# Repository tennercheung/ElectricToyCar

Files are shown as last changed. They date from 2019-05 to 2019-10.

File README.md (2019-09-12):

# ElectricToyCar

# (Car 1)
## ProtoV1

Code implemented with intent to test control with IR and on-board user controls of the vehicle

Encountered Issues:
* IR controls send different hex code stead FFFFFF when held in testing

## ProtoV1.1

Code implemented with intent to just the rider’s controls of the vehicle (speed & driving modes)

Encountered Issues:
* Motors shaking/jittery in fwd & bwd = PWM given to motor needs to start from low value so motors have time to speed up
* Motors run smoother independently -> since they are lower speeds there is less time needed to speed up
* When Arduino is reset, M2 is given power due to unallocated states of pins = since connected to LED takes a high during reset, reallocated pin 13 to pin 7

* Multiple buttons touched should keep system idle but instead triggers one/a mix of the button’s functions

## ProtoV2

Encountered Issues:
* Arduino must be **off** to send serial output to battery
* Battery has automatic shut off when pedal switch has not been pressed for longer than ~***10 minutes***
* When starting up the car, pedal switch is to be pressed first while the switch for power to the Arduino and H-Bridge (Red Switch on the back of the car) is off.
* 60kg servo does not function with the Arduino library, but works if it connects to the RC receiver
* Small servo jitters when RC is shut off
* Small detail, hidden speed control switch can be implemented as a small feature incase client wants to increase the speed of the car

# (Car 2)
## ProtoV1 
Encountered Issues: N/A

## Pedal Signal Analysis
Oscilloscope
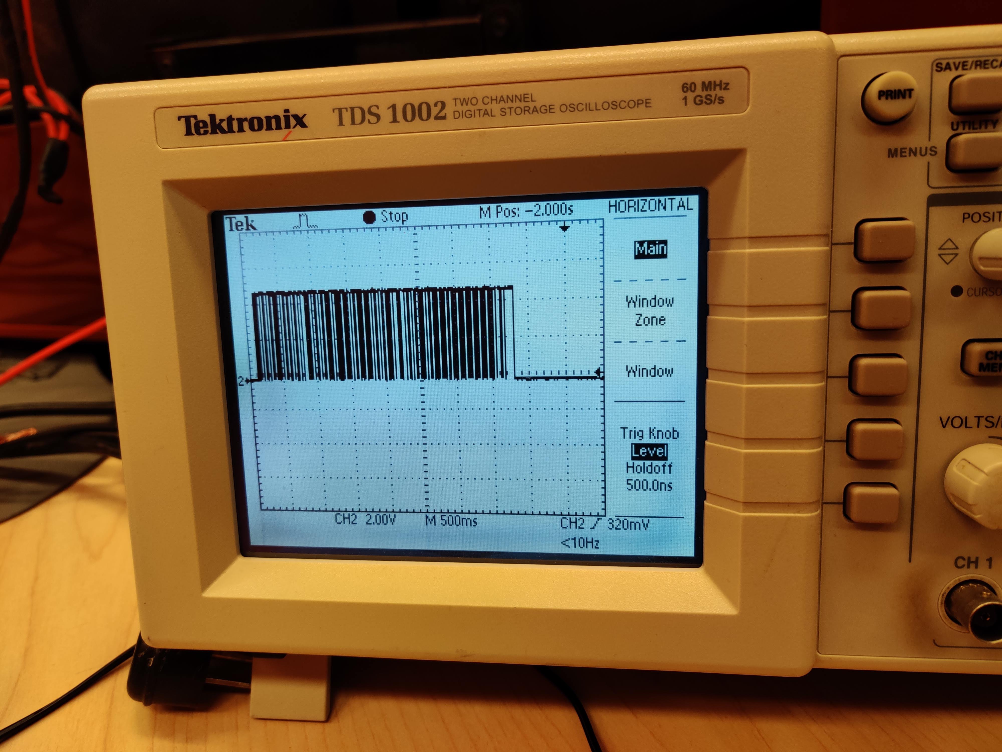
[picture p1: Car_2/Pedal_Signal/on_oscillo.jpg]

Serial Plotter
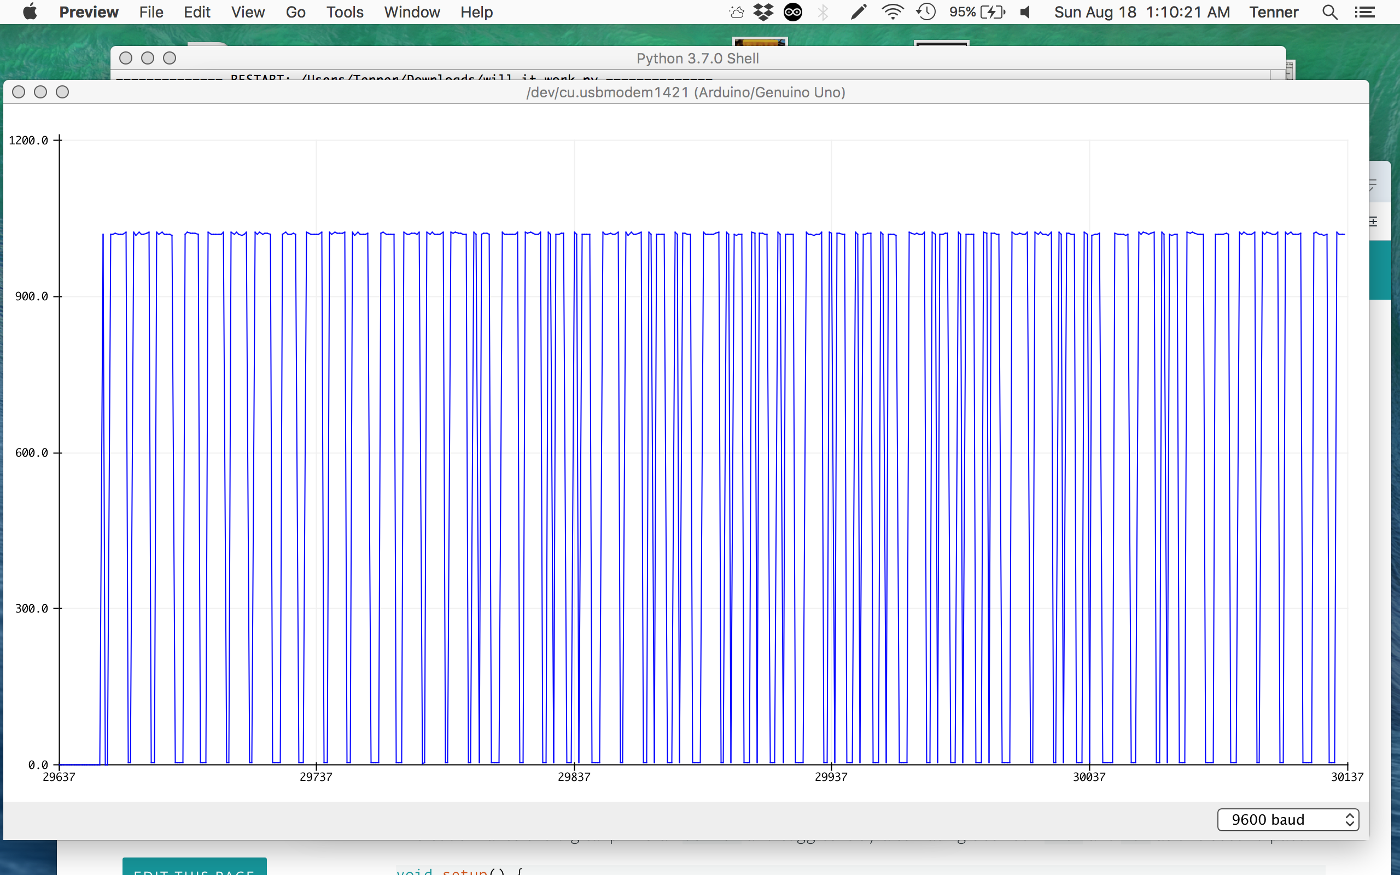
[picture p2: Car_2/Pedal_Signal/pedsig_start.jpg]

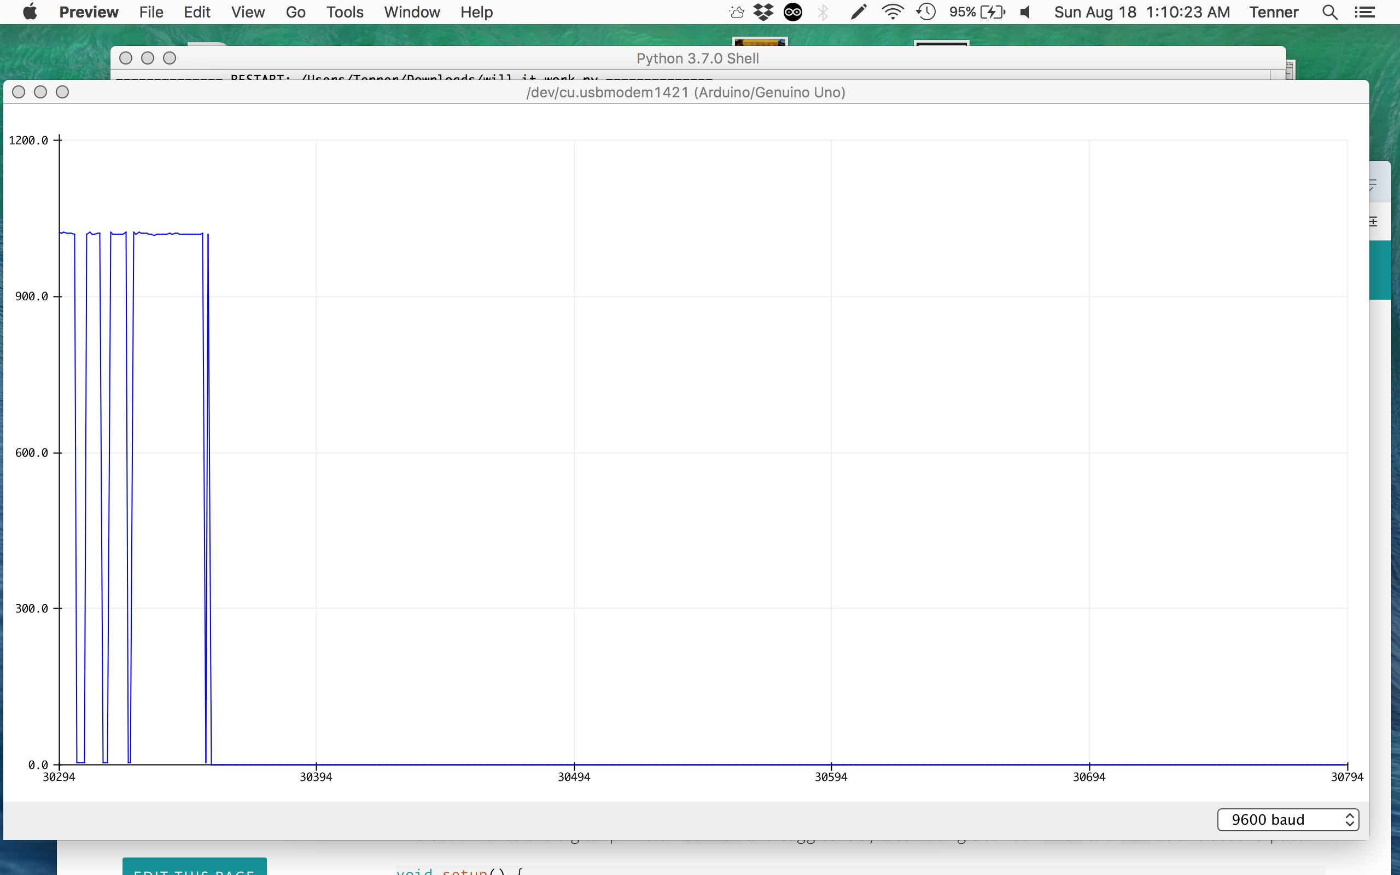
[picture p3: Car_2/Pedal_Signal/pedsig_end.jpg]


## Schematics

Motors
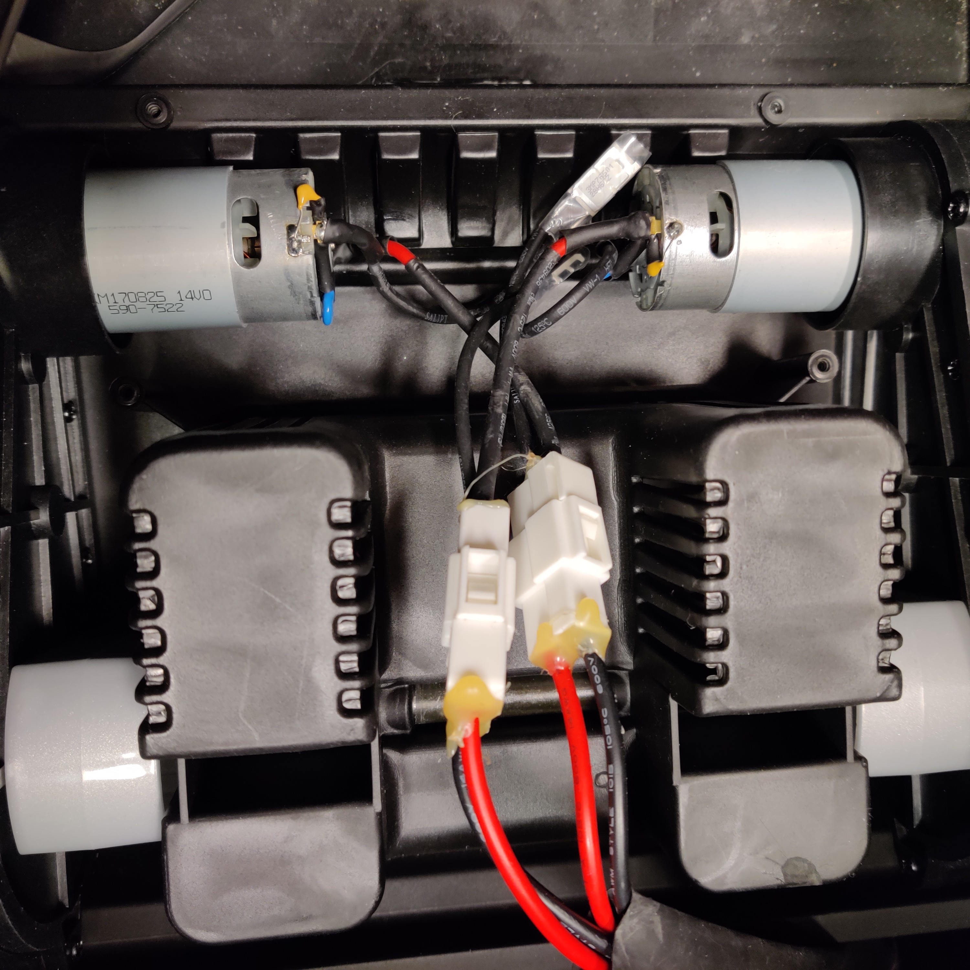
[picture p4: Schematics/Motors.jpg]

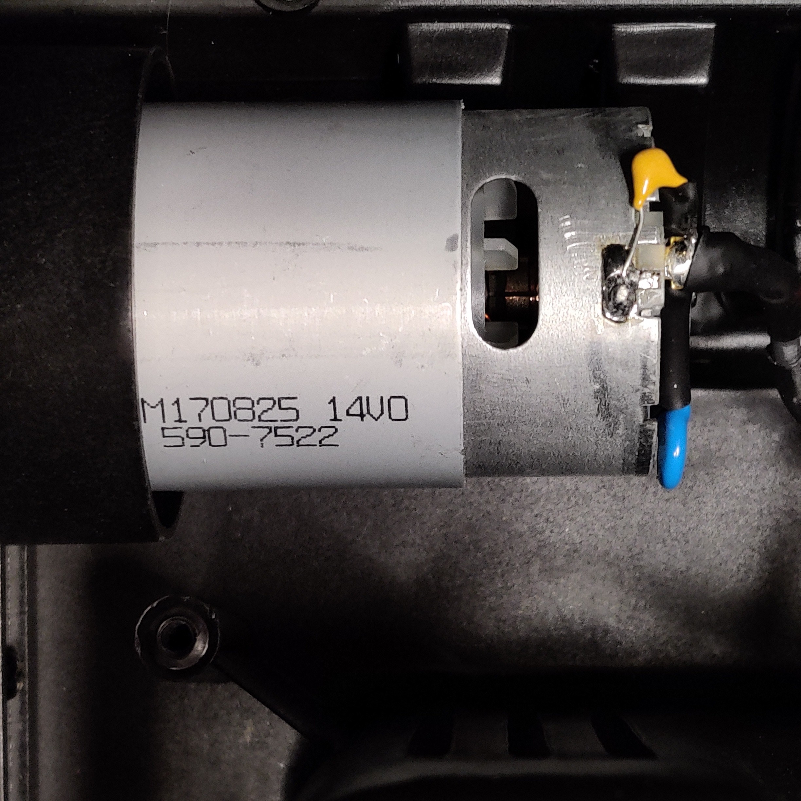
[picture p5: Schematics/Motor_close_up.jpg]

Dashboard PCB
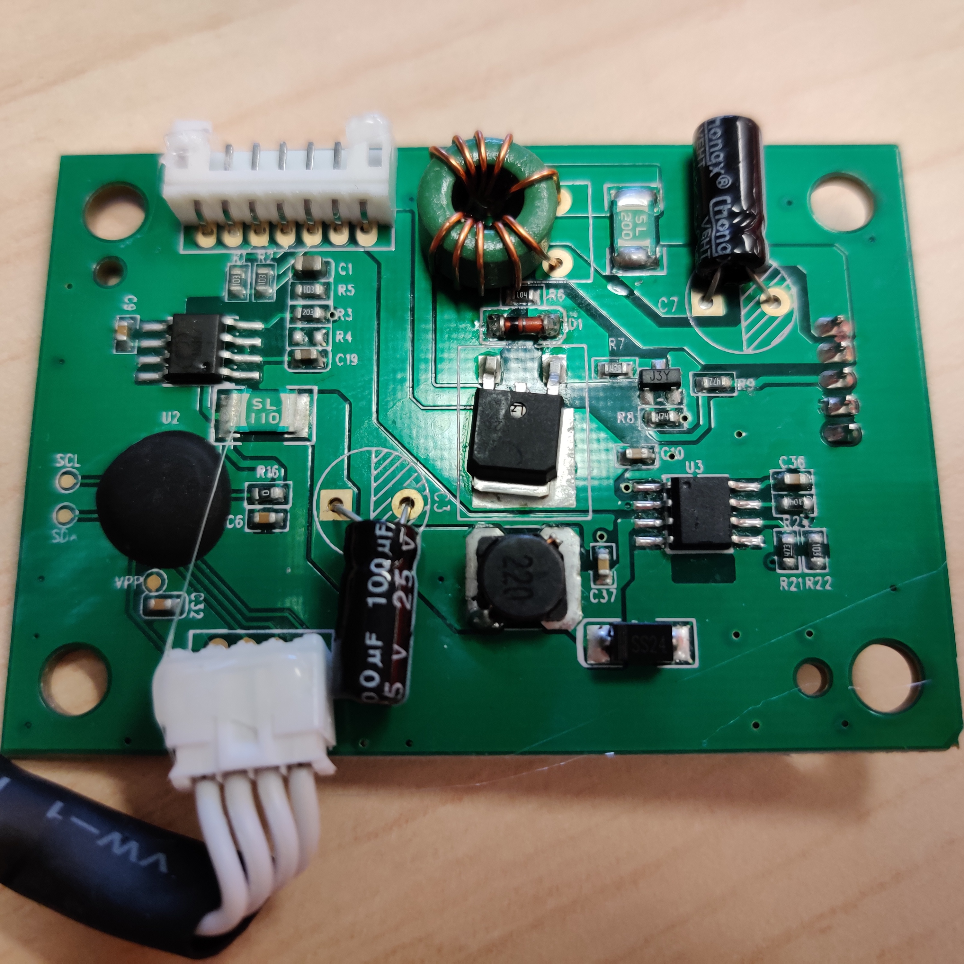
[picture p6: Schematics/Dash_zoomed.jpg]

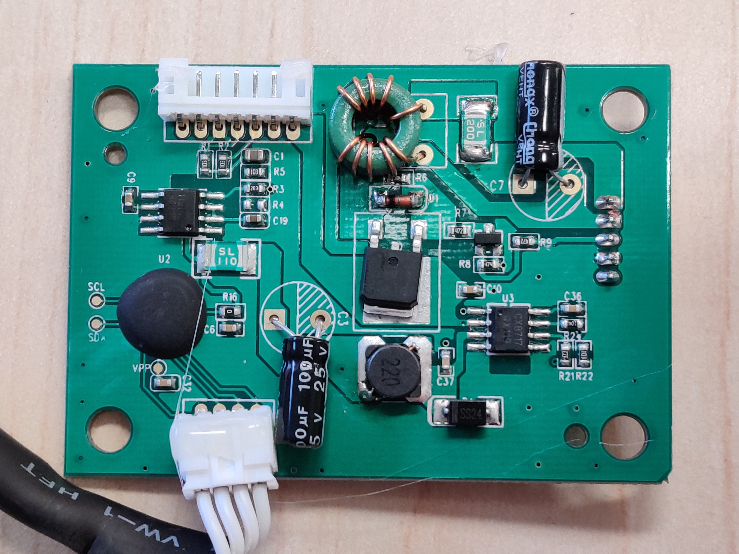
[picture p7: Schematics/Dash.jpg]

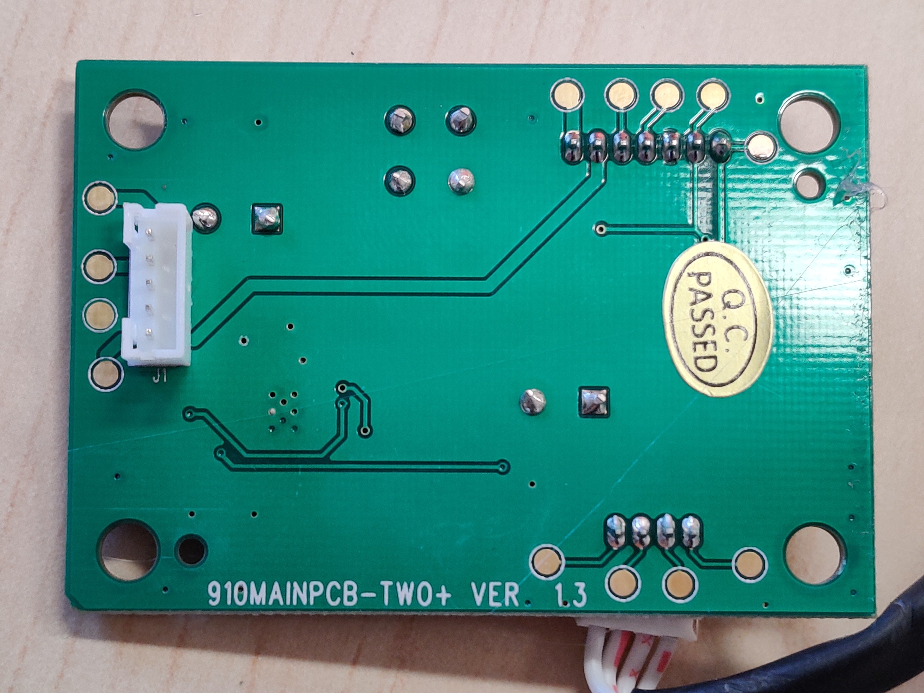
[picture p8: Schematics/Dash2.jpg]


## Useful Links:
* 7A/160W L298 Motor Board (https://amzn.to/2WCc6RT)
* Tesla Club Forum (https://bit.ly/2KY1rN8)

## Outline

1. Disassembled car by removing unnecessary wires in the dashboard and the pedal switch. **Black serial wire should be left untouched**.
2. Disconneted connectors from the motors and batteries. Used quick connects on 14 AWG wire, with a crimpping tool, to connect motor connectors to L298 Motor Board. Parallel connections are made from battery connectors to split power supply to pedal switch and to Vin of L298 Motor Board and Buck Converter. 
3. Modified switch that originally controlled the speed of the car to act as an on/off switch. Added a second parallel connection at the point before the Vin of the Buck Converter and Motor Board. *Refer to diagrams for parallel connections and on/off switch hookup*.
4. Implemented ciruit on Arduino Shield(s) (Car 1 has two Arduino Boards, Car 2 has one). For Car 1, Buck Converter has Vout split into parallel to supply power for both Arduinos. 
5. Mounted Arduino(s), Buck Converter, and L298 Motor Board in front storage compartment with M3 screws and stand-off spacers, drilled in holes through the bottom of the car for a nut to be attached on the spacers. Cut a hole for power supply wires to be routed inside the side of the car. 
6. On the bottom of the car two holes were drilled for the steering linkage and servo. Servo horn and steering linkage are secured with lock nuts.

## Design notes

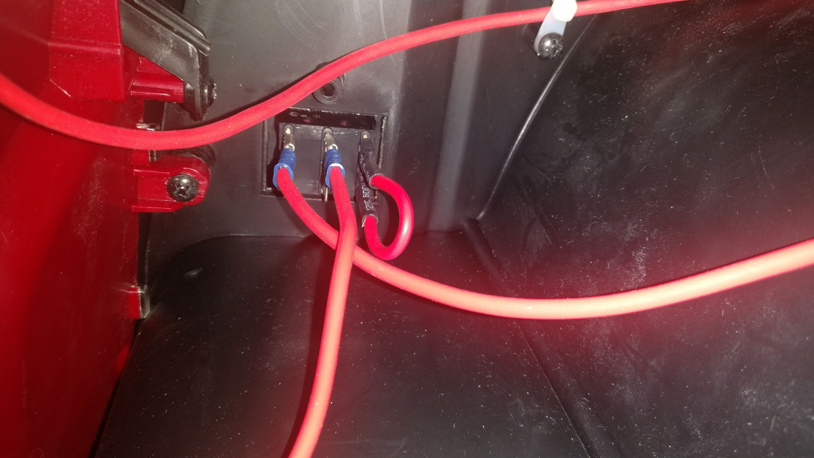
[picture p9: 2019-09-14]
Schematics/On_Off_Switch.jpg

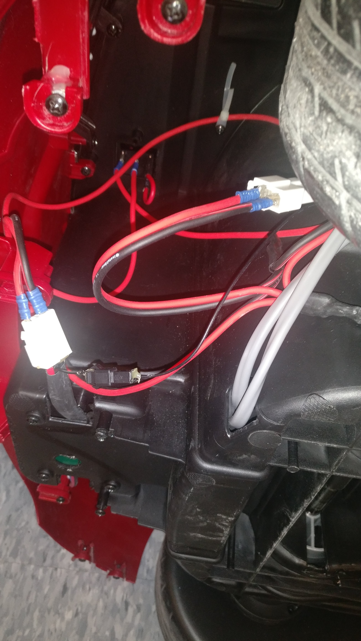
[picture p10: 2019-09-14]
Schematics/Pedal_and_Motor.jpg

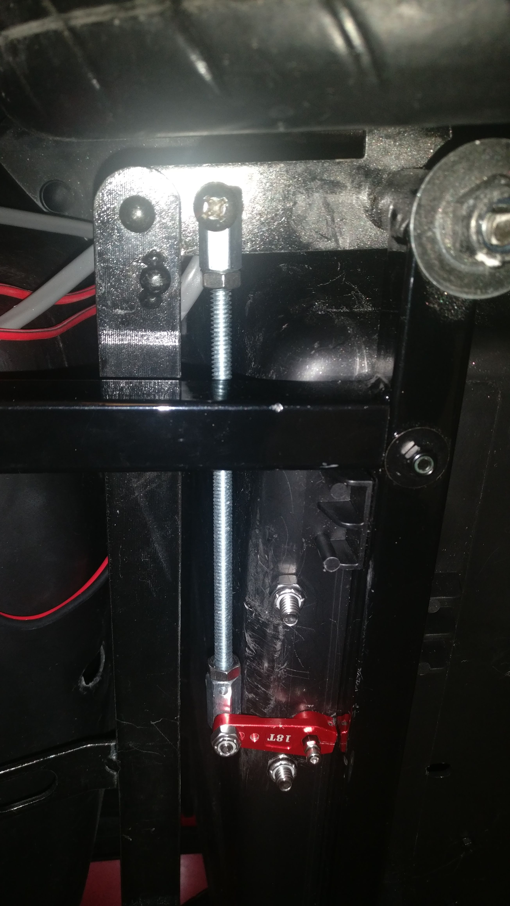
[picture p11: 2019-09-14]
Schematics/Steering_Linkage.jpg

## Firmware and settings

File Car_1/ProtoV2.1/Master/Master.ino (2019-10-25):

//
//#define analogPin A0
//int raw = 0;
//int Vin = 5;
//float Vout = 0;
//float R1 = 12000;
//float R2 = 0;
//float buffer = 0;
//
//void setup()
//{
//  Serial.begin(9600);
//  pinMode(2, OUTPUT);
//  pinMode(3, OUTPUT);
//  pinMode(4, OUTPUT);
//}
//
//void loop()
//{
//  raw = analogRead(analogPin);
//  if (raw)
//  {
//    buffer = raw * Vin;
//    Vout = (buffer) / 1024.0;
//    buffer = (Vin / Vout) - 1;
//    R2 = R1 * buffer;
////    Serial.print("Vout: ");
////    Serial.println(Vout);
////    Serial.print("R2: ");
////    Serial.println(R2);
//  }
//  if (R2 > 5600 and R2 < 6600) {
//    analogWrite(3, 0);
//    digitalWrite(2, HIGH);
//    digitalWrite(4, LOW);
//  }
//  else if (R2 < 5600 and R2 > 4200) {
//    analogWrite(3, 0);
//    digitalWrite(2, LOW);
//    digitalWrite(4, HIGH);
//  }
//
//  else {
//    analogWrite(3, 255);
//  }
//}


/*

  M1:
  IN1 = 8, IN2 = 9
  EN1 = 6
  M2:
  EN2 = 11
  IN3 = 10, IN4 = 7
*/

//M1:
#define IN1 8
#define IN2 9
#define EN1 6

//M2:
#define IN3 10
#define IN4 7
#define EN2 11

#define steerOUT 5

#define steerPin A0
#define CH1 A1
#define CH2 A2

#define FORWARD 1
#define BACKWARD 2

#define LEFT 3
#define RIGHT 4
#define CENTRE 5
#define LEFTBWD 6
#define RIGHTBWD 7
int speed = 50;
int turnDirection;
int ch1;
int ch2;

int steerval;
int raw = 0;
int Vin = 5;
float Vout = 0;
float R1 = (12*1000);
float R2 = 0;
float buffer = 0;

void change_direc (bool direct) {
  if ((direct == HIGH || direct == LOW)) {

    digitalWrite(IN1, !direct);
    digitalWrite(IN2, direct);
    digitalWrite(IN3, direct);
    digitalWrite(IN4, !direct);
  }
}

void run_motors (int speed, int direc) {
  

  if (direc == 1) {
    analogWrite(EN1, speed);
    analogWrite(EN2, speed);
    Serial.println("  fwd active  ");
    change_direc(HIGH); //forward //high
  }

  else if (direc == 2) {
    analogWrite(EN1, speed);
    analogWrite(EN2, speed);
    Serial.println("  bwd active  ");
    change_direc(LOW); //backward //low

  }
  else if (direc == 3) {
    analogWrite(EN1, speed*1.25);
    analogWrite(EN2, speed*0.75);
    change_direc(HIGH);
  }
  else if (direc == 4) {
    analogWrite(EN1, speed*0.75);
    analogWrite(EN2, speed*1.25);
    change_direc(HIGH);
  }
  else if (direc == 6){
    analogWrite(EN1, speed*0.75);
    analogWrite(EN2, speed*1.25);
    change_direc(LOW);
  }
  else if (direc == 7){
    analogWrite(EN1, speed*1.25);
    analogWrite(EN2, speed*0.75);
    change_direc(LOW);
  }
}

void motor_off () {
  analogWrite(EN1, 0);
  analogWrite(EN2, 0);
}


void setup()
{
  Serial.begin(115200);
  pinMode(2, OUTPUT);
  pinMode(3, OUTPUT);
  pinMode(4, OUTPUT);

  pinMode(IN1, OUTPUT);
  pinMode(IN2, OUTPUT);
  pinMode(EN1, OUTPUT);

  pinMode(IN3, OUTPUT);
  pinMode(IN4, OUTPUT);
  pinMode(EN2, OUTPUT);

  //pinMode(CH1, INPUT);
  pinMode(CH2, INPUT);

  pinMode(steerOUT, OUTPUT);
}

void loop() {
//  ch1 = pulseIn(CH1, HIGH, 25000);
  delay(12);  ch2 = pulseIn(CH2, HIGH, 25000);

//  int steermap = map((analogRead(steerPin)), 0, 1023, 0, 180);
//  steerval = analogRead(steerPin);

//  raw = analogRead(steerPin);



//  if (raw) {
//    buffer = raw * Vin;
//    Vout = (buffer) / 1024.0;
//    buffer = (Vin / Vout) - 1;
//    R2 = R1 * buffer;
//  }

  if (ch1 > 2000) {
    analogWrite(steerOUT, 255);
    turnDirection = RIGHT;
  }
  else if (ch1 < 1470 and ch1 != 0) {
    analogWrite(steerOUT, 0);
    turnDirection = LEFT;
  }
//  else if (R2 > 6600){
//    analogWrite(steerOUT, 255);
//  }
//  else if (R2 < 4200){
//    analogWrite(steerOUT, 0);
//  }
  else {
    analogWrite(steerOUT, 120);
    turnDirection = CENTRE;
  }
//
//  if (R2 >= 5600 and R2 < 6600) {
//    analogWrite(3, 0);
//    digitalWrite(2, HIGH);
//    digitalWrite(4, LOW);
//  }
//  else if (R2 < 5600 and R2 > 4200) {
//    analogWrite(3, 0);
//    digitalWrite(2, LOW);
//    digitalWrite(4, HIGH);
//  }
//
//  else {
//    analogWrite(3, 255);
//  }

    if (ch2 > 2010) {
      if (turnDirection == LEFT){
        run_motors(speed, LEFT);
      }
      else if (turnDirection == RIGHT){
        run_motors(speed, RIGHT);
      }
      else if (turnDirection == CENTRE){
        run_motors(speed, FORWARD);
      }
  }
  else if (ch2 < 1400 and ch2 != 0) {
      if (turnDirection == LEFT){
        run_motors(speed, RIGHTBWD);
      }
      else if (turnDirection == RIGHT){
        run_motors(speed, LEFTBWD);
      }
      else if (turnDirection == CENTRE){
        run_motors(speed, BACKWARD);
      }
  }

  else { //run idle
    motor_off();
  }
}

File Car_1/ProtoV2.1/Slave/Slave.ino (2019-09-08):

// Servo library
#include <Servo.h>
#define STEER 6

#define steerIN A3
#define posHome 80
#define posLeft 60
#define posRight 100
//50, 110
Servo steer;
boolean steerCheck[3] = {true, false, true};
int analogNum;
int currentSteer;
void setup() {
  Serial.begin(115200); // Pour a bowl of Serial

  steer.attach(STEER);  // attaches the servo on pin 9 to the servo object
  steer.write(posHome);
}

void loop() {
  analogNum = analogRead(steerIN);
  currentSteer = steer.read();
  Serial.println(currentSteer);
  Serial.println(analogNum);
  if (analogNum > 500) {
    steerCheck[2] = steerCheck[1];
    steerCheck[1] = steerCheck[0];
    steerCheck[0] = true;

  }
  else if (analogNum < 500) {
    steerCheck[2] = steerCheck[1];
    steerCheck[1] = steerCheck[0];
    steerCheck[0] = false;
  }
  if (steerCheck[0] == true and steerCheck[1] == true and steerCheck[2] == true) {
    if (currentSteer < posRight){
      steer.write(currentSteer + 1);
    }
    else if (currentSteer > posRight){
      steer.write(currentSteer - 1);
    }
    else if (currentSteer == posRight){
      steer.write(currentSteer);
    }
    
  }
  else if (steerCheck[0] == false and steerCheck[1] == false and steerCheck[2] == false) {
    if (currentSteer > posLeft){
      steer.write(currentSteer - 1);
    }
    else if (currentSteer < posLeft){
      steer.write(currentSteer + 1);
    }
    else if(currentSteer == posLeft){
      steer.write(currentSteer);
    }
  }
  else {
    if (currentSteer > posHome){
      steer.write(currentSteer - 1);
    }
    else if (currentSteer < posHome){
      steer.write(currentSteer + 1);
    }
  }
}

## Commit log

2019-05-07 updated prototype 1 code
2019-05-07 added attempt at holding IR buttons
2019-05-12 fixed issues with fwd & bwd running
    [ProtoV1.1.ino]
2019-05-31 added pic of motors
2019-06-02 fixed issue w/IN4 HIGH at reset
    [ProtoV1.1.ino]
2019-06-15 added steering
2019-06-15 added user steering
2019-06-15 added rc motor movement
2019-06-16 partial throttle control
2019-06-16 added template buttons
2019-06-18 added rc control for bidirectional throttle
2019-06-24 added current vehicle code
2019-06-26 added differential steering & improved power steering angles
2019-08-10 added RC throttle control
2019-08-10 changed throttle bounds
2019-09-16 Fritizing Circuit Diagram
    https://github.com/yohendry/arduino_L298N, for L298N board
    [Electric_Ride_On_Car.fzz]
2019-10-25 Commented Out Channel 1, servo
